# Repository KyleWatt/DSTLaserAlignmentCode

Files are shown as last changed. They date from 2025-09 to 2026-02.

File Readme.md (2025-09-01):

# Laser Auto-Alignment for FSOC Systems

Automated 3-axis alignment platform for Free Space Optical Communication systems using stepper motors and intelligent search algorithms.

## Features

- Sub-micron precision alignment (0.666μm steps)
- Dual search algorithms (Raster & Spiral scanning)
- Custom PCB controlling 12 stepper motors
- Real-time power optimisation
- 3D-printed mechanical components

## Hardware

- **MCU:** Raspberry Pi Pico 2350 B
- **Motors:** 12x 28BYJ-48 steppers with A4988 drivers
- **Power:** 12V input, 3.3V regulation
- **Materials:** PLA 3D-printed parts

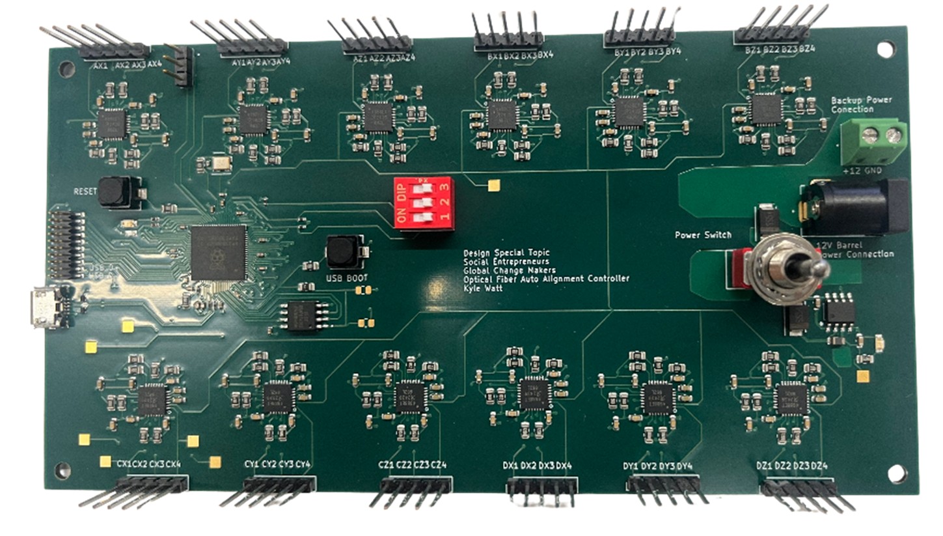
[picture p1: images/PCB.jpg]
PCB Image

*Custom PCB with RP2350B microcontroller and 12 A4988 motor drivers*

## Quick Start

1. Flash firmware to RP2350B
2. Assemble the mechanical system from the STL files
3. Connect via USB terminal (PuTTY/Tera Term)
4. Use the 'help' command for a detailed explanation of functions/commands
5. Run alignment algorithms: `raster`, `spiral', 'SPGD', or align with manual adjustments through manual mode or enter a control loop for continuous optimisation in automatic mode

### Manual Control
```
manual          # Enter manual control mode
centre          # Return to centre position
move x y z      # Move to specific coordinates
```

### Algorithms
```
raster <width> <height_shift> <iterations>
spiral <turns> <spacing> <points>
SPGD <iterations> <offset_range> <learning_rate> <threshold>
```

## Repository Structure

```
├── PCB/           # Schematics, gerbers, BOM
├── src/          # Firmware source
├── mechanical/    # 3D model files
└── docs/          # Detailed documentation
```

## Performance Results

| Algorithm | Starting Power | Peak Found | Improvement |
|---|---|---|---|
| Raster | -23.01 dBm | -4.89 dBm  | 18.12 dB |
| Spiral | -8.99 dBm | -6.21 dBm  | 2.78 dB |

## PCB Design

Custom 160mm × 80mm board with:
- 6-layer stackup for signal integrity
- Switching power regulation
- EMI mitigation design
- Test points for debugging

Design files and manufacturing documentation available in `/PCB` directory.

## Software Architecture

- **Dual-core processing:** Motor control + power monitoring
- **Struct-based design:** Position tracking and optimization
- **Memory function:** Automatic return to peak power positions
- **Real-time feedback:** Power monitoring during alignment

See [full technical report](docs/full_report.pdf) for detailed performance analysis and design decisions.

## Team

- **Kyle Watt:** PCB design, software development
- **Rory Mullen:** Mechanical design, prototyping  
- **Tamim Abdul Maleque:** Component sourcing, assembly

**Supervisors:** Professor Martin Lavery, Adam Vallance, Mark Main

*University of Glasgow - School of Engineering - 2024/25*

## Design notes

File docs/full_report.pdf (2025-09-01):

## ENG 5026: Design Special Topic 5 Laser Auto-Alignment for Communication Systems in the

Developing World.

## Report Written By:

Kyle Watt,
Rory Mullen,

## Tamim Abdul Maleque

2024/25

## Supervisors: Professor Martin Lavery, Adam Vallance, Mark Main

## Acknowledgment

We would like to extend our gratitude to Mark Main, Adam Vallance for their continuous support with technical support and laboratory guidance. We are also grateful to Professor Martin Lavery for the advice of the project and for allowing us to use the facilities of his Structured Photonics Group.

## Abstract

In this DST project, the development and evaluation of a compact, low-cost motorised auto-alignment platform for free-space optical communication (FSOC) system was designed to mitigate the effects of temperature and pressure fluctuations that impact the optical alignment of the fibres in the FSO system. A mechanical assembly done using 3D-printed PLA, which includes a X-Y flexure controlled a lead-screw mechanisms (which have a 0.20 mm pitch, hence a minimal step size of approximately 0.666 µm per rotation) using the, by the off-the-shelf 28BYJ-48 stepper motors and A4988 drivers for a automated alignment. A mechanical design connecting the Z-axis alignment with XY flexure was done using 3D-designed and printed runners, which also operated using a lead-screw mechanisms and used a cheap threaded steel 4-inch driveshaft. A purpose purpose-designed PCB was done where the Raspberry Pi Pico 2350 B microcontroller used a raster and spiral scan algorithm-based control to search and find the optimum power level. The raster and spiral algorithms were tested both to great success, with both scanning over areas with both high and low optical power before settling on the peak. This project shows that each of the algorithms is far superior to manual control at identifying and aligning the FSOC system with more precision.

## Contents

## Introduction

The internet is a vital need to billions of people in the world. Internet access fosters economic growth, security and technological developments in digital technology & artificial intelligence [1]. However, there is a stark digital divide globally, with an estimated 2.6 billion people remaining unconnected according to the 2023 press release article by International Telecommunication Union [2]. This divide affects developing nations because of the limitations of infrastructure and associated costs in deployment of traditional fibre optic cables, in geographically challenging or sparsely populated rural areas. As highlighted in the discussion on tackling Africa's digital divide, the capital cost of fibre can go upwards of US$100,000 per kilometre, which creates an economic barrier due to initial fibre infrastructure establishment [3].
Furthermore, even when deployed, fibres in remote regions can be susceptible to damage from environmental factors or theft, hence increasing the barriers for socio-economic progress. This limitation of connectivity necessitates the use and development of cost-effective alternative technologies to bridge the digital divide, using Free Space Optical Communication (FSOC).
Free Space Optical Communication (FSOC) transmits data through the atmosphere using beams of light, typically in the infrared (IR) spectrum, which is an alternative to traditional cabled solutions [3]. Conceptualised as ‘fibre optics without the fibre’ FSOC offers the potential for gigabits per second (Gbps) data rates [4]. This high capacity is due to the vast, typically unregulated bandwidth available at optical frequencies (Near IR region wavelengths: 850nm, 1310nm, and 1550nm). Therefore, the optical spectrum offers bandwidths that are orders of potentially tens of terahertz (THz) across various windows if compared to entire radio frequency (RF) spectrum, where individual services are allocated bandwidth typically measured in megahertz (MHz) or gigahertz (GHz). The RF spectrum is also often licensed by regulatory bodies.
The theoretical upper bound on the information rate that can be transmitted over a communication channel is given by the Shannon-Hartley theorem, which states that the channel capacity (C), in bits per second, is C=B × log2(1+S/N), where B is the bandwidth of the channel in hertz, S is the average received signal power, and N is the average noise power [5].Increasing bandwidth can increase channel capacity although not limitless as the relationship between signal to noise ratio is a constraint and other practical limitations such as power, dispersion and system integration need to be considered.
Recognising the potential of FSOC, the practical deployment of the systems is met with operational challenges. A primary concern, once an initial line-of-sight is established, is the maintenance of precise optical alignment between the transmitter and receiver [6]. The stability of this alignment is important for maintaining link performance, as very small deviations can lead to significant signal loss or complete link failure, especially as distance between transceivers increase. But, how are these issues arising? FSOC systems are susceptible to mechanical misalignments from sources such as thermal changes of mounting structures due to daily and seasonal temperature fluctuations, wind effects on buildings or structures where the equipment is housed and mechanical vibrations present in the physical world [4].
Narrow beam divergence which is inherent in laser-based communication makes precise pointing accuracy extremely important for FSOC. Pointing accuracy requirements can be on the order of several hundred microradians. Atmospheric effects such as turbulence (causing signal scintillation and beam wander) and attenuation due to fog or haze also impact long distance FSOC performance [4][6]. These atmospheric phenomena can cause the laser beam's intensity to fluctuate unpredictably, its path to deviate from the direct line-of-sight, and its overall power to diminish significantly before reaching the receiver, all of which degrade the quality and reliability of the communication link
Previously, for the FSOC set-up at University of Johannesburg, correcting such fine misalignments has required manual intervention, delicate screw adjustments using costly high-precision commercial components (Thorlabs XY Translation Mounts – costing approximately £170 each). This reliance on manual recalibration not only increases operational expenditure but also introduces delays in restoring connectivity, which impacts accessibility and scalability of FSOC solutions, especially in resource-limited settings.
To address the solution of mechanical misalignment and reduce costly manual recalibration in FSOC systems, this project focused on developing an entirely 3D printed compact, motorised auto-alignment system for XYZ axis. Using Commercial Off-The-Shelf (COTS) components to create the system accessible, affordable and easily replicable solution would hence democratise access to stable FSOC systems. Primary tasks of the auto-alignment use precise motorised control (using stepper motors), for fine adjustments. Such a system will operate in three axes:
- X-Y Adjustment: Provides angular correction crucial for coupling light into optical fibres (often with core diameters around 100µm).
- Z-Axis Adjustment: Optimises beam focus or collimation, vital for maximising received signal power, especially over longer distances where beam divergence is a factor.
The auto-alignment system is algorithm-based, that uses search patterns to locate and optimise the optical signal. Two common algorithms used in auto-alignment solution are Raster Scanning and Spiral Scanning [7] as depicted in Figure 1 below. Raster

Scanning is often one of the quickest methods for initially finding the beam at the receiver ("first light"). It operates by scanning along one axis (x-axis) and then indexing by a certain distance along another (y-axis), repeating this cycle. The advantage in this method is the utility for finding the threshold power detection (above -25dBm) and for subsequent search to find peak power optimisation. This method is limited to two-axis operation and involves discrete start-stop motions.
An additional method of Spiral Scanning executes an outward spiral motion, where it too can be used to find the first light in a larger general area of the beam and search for highest power position after completing the spiral. Continuous spiral scans offer smoother motion, where in computer programme the spiral code is described in polar coordinates (r, θ). This method is also limited to two-axis operation and requires completion of the entire trajectory described in space.

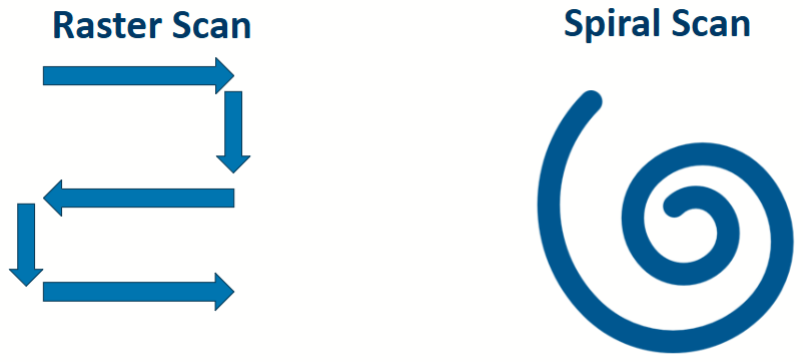
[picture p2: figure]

Figure 1: Illustration of search patterns used in FSO auto-alignment. (Left) Raster Scan Pattern and (Right) Spiral Scan Pattern.

The development of a cheaper and better commercially available auto-alignment solution makes FSOC a more practical as and sustainable solution for a more range of applications. For example, these portable self-aligning systems can be highly advantageous for providing emergency connectivity during disaster situations when terrestrial infrastructure is compromised [4] [6].
FSOC systems effectively address the "last mile" connectivity challenge, bridging the final network gap to end-users where fibre installation is often costly and complex [3][4]. Compared to fibre, deploying FSOC transceivers on existing structures like rooftops is less complex, and they can be integrated into hybrid communication networks with RF or fibre links to enhance overall reliability [3] [4]. These advantages enable rapid FSOC deployment, providing high-speed digital links to remote and rural communities while overcoming obstacles related to terrain, installation costs, infrastructure security and so bridging the digital divide [3] [4].

While transient obstructions might cause brief interruptions, the high bandwidth of FSOC links and multiple channels can mitigate the impact on many common internet activities. The deployment of such enabling technology also aligns strongly with several United Nations Sustainable Development Goals (UN SDGs), by fostering economic growth (UNSDG 8), promoting innovation and infrastructure (UNSDG 9), and reducing inequalities (UNSDG 10).

## Project Management

As a three-member team, communication was facilitated through MS Teams and WhatsApp, with a primary emphasis on in-person meetings. Work delegation was a collaborative effort, involving regular communication and consultation with supervisors, Mark and Adam.
Recognising the importance of early prototyping, the team initiated this process alongside printed circuit board (PCB) design. Electronic components were sourced with a focus on cost-effectiveness and global availability.
The Structured Photonics Group’s laboratory's 3D printing facilities were utilised for rapid prototyping and assembly of the mechanical system, enabling iterative testing and refinement. Algorithm work was completed in parallel with PCB design, ensuring that GPIO pins and electronic requirements were matched. The work was then performed in an optics laboratory on an optical table for testing of the full mechanical system with the algorithm written. A flowchart of the full process in this project is shown in figure 2 below.

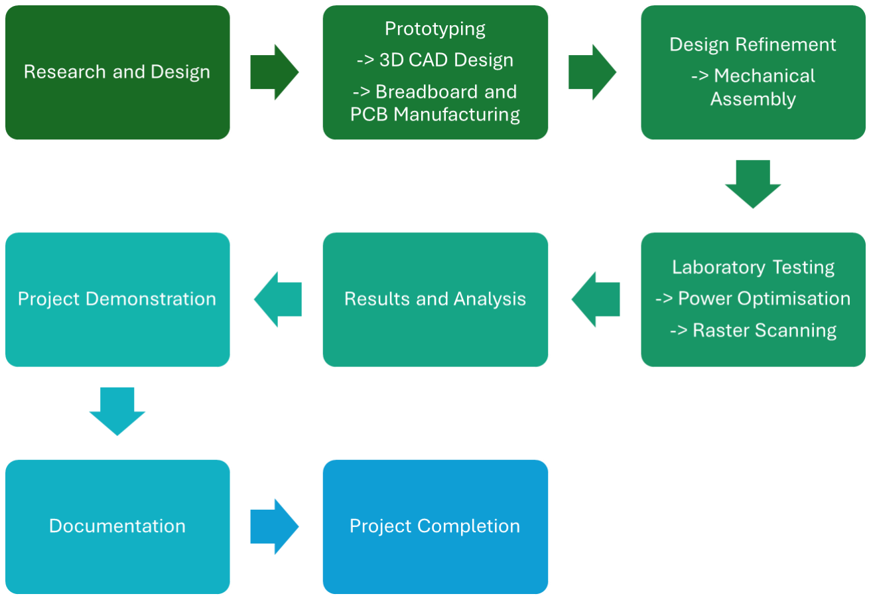
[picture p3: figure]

Figure 2: The Design Build and Test Project Flowchart of this project.

While the project successfully met its primary objectives, an area for improvement in project management would have been to maintain a more consistent pace of progress throughout the semester.

## PCB Design

## Requirements and Justification

The PCB was one of the earliest components developed in this project, based on the advice that manufacturing and debugging would require as much time as possible. A custom PCB was essential, as the project aimed to control four optical fibres' X, Y, and Z movements, requiring 12 motors. Without a PCB, the system would be significantly less compact, more challenging to assemble and maintain, and more prone to errors due to increased wiring complexity.
Additionally, designing a PCB made the system more reproducible. If successful, this design could be easily replicated and deployed by communities, providing them with internet access at a low cost and greater control over how that access is delivered.

## Components selection

One of the key criteria in selecting components for the PCB was ensuring that they were widely available and low-cost. This would make the design easily reproducible and affordable, allowing deployment in areas that cannot support the cost of traditional high-speed communication infrastructure.
Motor Driver
The first components selected were the motor drivers. We chose the A4988 stepper motor driver [8] because it was inexpensive (under £1) and readily available—both critical requirements. However, we encountered a challenge: each A4988 has eight input pins, and with 12 stepper motors, this would require up to 96 GPIO pins on the microcontroller - an impractical number.
To address this, we decided to minimise the number of active control inputs to each A4988. Pins that did not need to change dynamically were hard-wired to either high or low. Since micro-stepping was unnecessary, the associated pins (MS1, MS2, MS3) were grounded. Additional features such as reset and sleep were also deemed unnecessary, so these active-low pins were connected to 3.3V.
The only pins connected to the microcontroller were those essential for basic operation: step, direction, and enable.
➔ The step and direction pins are critical for controlling motor movement.
➔ Although not required for motion, the enable pin was retained to allow the microcontroller to turn off motors when idle, reducing power consumption, which was a key consideration for sustainability.

Motor
The selected motor was the 28BYJ-48 5V stepper motor [9], chosen for its low cost (~£6) and wide availability, both key selection criteria. However, a challenge arose: this motor has a unipolar configuration, while the chosen driver, the A4988, is designed for bipolar stepper motors.
Unipolar motors have a centre tap on each coil, allowing current to flow in one direction per coil half, which simplifies driving but results in lower torque. In contrast, bipolar motors lack a centre tap and require current reversal through each coil, making them more complex to drive but offering higher torque and better efficiency.
To address this mismatch, the centre tap (power) wire of the 28BYJ-48 was left unconnected, effectively converting it to bipolar mode, which allows it to work with the A4988 driver.
While the 28BYJ-48 does not offer high precision, this limitation is compensated by the mechanical design, which enables step sizes as small as 0.6 µm even without microstepping.
Power System
The power system used a 12V Barel jack input with a backup screw terminal, to allow it to be powered by a bench power supply. The 12V was adequate to allow functionality for the A4988 Stepper Driver, as it can function with load voltages up to 35V; however, all other components required a supply of 3.3V.
This meant the power had to be stepped down from 12V to 3.3V. To do this, we used the AP1509-33SG-13. The AP1509-33SG-13 was chosen as it is a switching regulator, meaning the energy loss to heat would be minimal. The other reason for selecting the AP1509-33SG-13 was its simplicity in converting to 3.3V from 12V, as it only required two capacitors, an inductor and a Schottky diode.
Microcontroller
The microcontroller chosen for this project was the Raspberry Pi Pico 2350 B. Again, the main reason for selecting this component was its low price and wide availability. On top of the low cost and wide availability, the Pi Pico 2350 B also has the added advantage of having 80 GPIOs, which is extremely useful for our requirements of 12 motors. An extra feature beneficial with the Pi Pico 2350 B was its ability to use multicore processing. This means that multiple processes can run in parallel; therefore, if any functions need to wait, they could be run in parallel and not block other processes.

Communication/Controls
Some final components that were added to improve the ease of use and future development of the board were DIP Switches, allowing for external control of operation and modes/algorithms used. It was also decided we would add a micro-USB port to the flash firmware of the Pi Pico 2350B to allow easy communication with external devices. TVS diodes were connected to the USB data lines (D+ and D−) to clamp high-voltage spikes caused by ESD or power surges, preventing damage to the USB transceiver or microcontroller. Since USB lines are exposed and can easily accumulate static electricity (e.g. from plugging/unplugging), TVS diodes help ensure reliable operation and extend device lifespan.
Simple LEDs were also chosen to help with debugging code and hardware. Also, male headers were connected to the motor drivers and GPIO pins to allow for external communications. All the other components chosen followed the previously mentioned components' datasheets.

## Schematic Design and Evaluation

The PCB was designed using KiCAD, a cross-platform and open-source electronic Design Automation Suite. The initial steps in the PCB design were to create a schematic.
RP2350B
The recommended design from the “Hardware Design with RP2350” [10] manual was followed when designing the schematic for the RP2350B, and all essential components for operation, such as the recommended oscillator and flash memory, were added following the manual. This can be seen in Figure 3 in the next page.

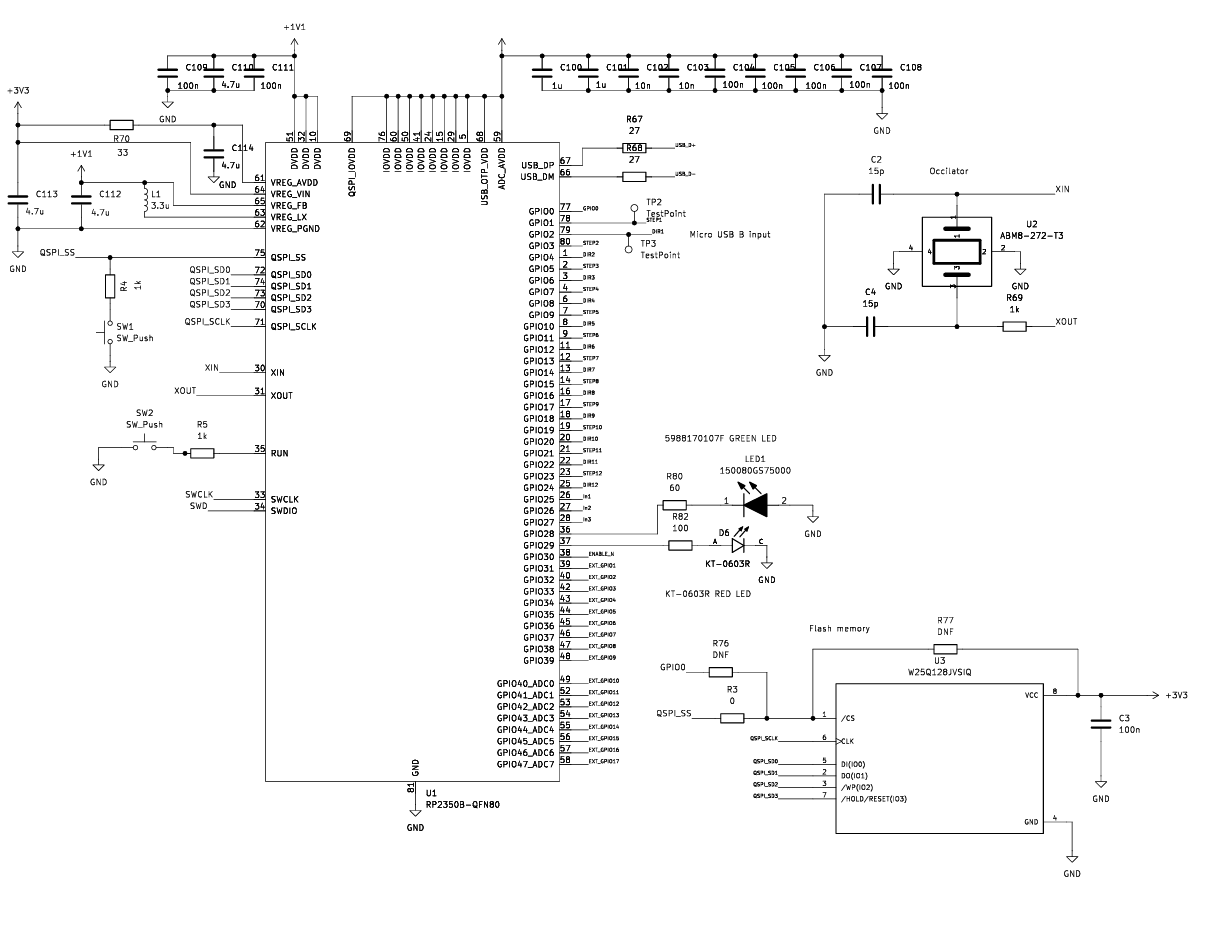
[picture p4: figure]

Figure 3: The 2RP2350B IC Schematic utilised in the PCB design.

As can be seen by Figure 3, the first 24 pins are used to control the step and direction of all motor drivers, and one pin, 30, is used to control the Enable function on all motor drivers. All other GPIOs were connected to allow external communication, such as buttons, LEDs and headers.
Motor Drivers
The next components are designed in the schematic, where the motor drivers are. As previously mentioned, the aim was to reduce the number of GPIO pins necessary to control the motor driver while still maintaining complete functionality. This was done by pulling all non-essential pins high or low, depending on whether they are active high or low. The A4988 was also configured to limit the maximum current to around 1 amp as higher current could potentially cause issues with the motors. This was done by configuring the reference voltage and sense resistors. In this case, the reference voltage (Vref) was 1.65V, and the sense resistors (RS), Sense 1 and Sense 2, were 0.2 Ohms.

Max Current =

Vref
8 × RS ≈ 1Amp (1)

All of which can be seen in Figure 4. The outputs of the motor driver OUT1A/1B/2A/2B were all connected to a male header, allowing for easy connection to the 28BYJ-48 5V Stepper Motor.

Figure 4: The Motor Driver 3 A4988 Schematic Design utilised in the PCB design.

Power
As previously mentioned, the majority of components required a 3.3V supply, and to achieve this, the AP1509-33SG-13 was used to step the power down from 12V to 3.3V. This followed the simple design outline in the AP1509-33SG-13 data sheet. However, a resistor and LED were added to indicate if the AP1509-33SG-13 was functioning as expected and producing 3.3V. Test points were also added all around the board in vital areas, such as the output from the AP1509-33SG-13, to help the debugging process. The test points were also added to other vital areas, such as the step and direction pins and the output from the A4988.

## PCB Design

Board Dimensions and Stack-up
After completing the schematic, it was reviewed with the assistance of Adam Valance and Mark Main. To ensure accuracy, all design elements were carefully evaluated and cross-referenced with the component datasheets.
Once the schematic was finalised, the next step was to design the PCB. I chose a
160 mm × 80 mm board size, as there were no constraints on dimensions. This provided sufficient space to accommodate all 12 motor drivers while also ensuring adequate separation between high-EMI components like the switching regulator and sensitive data lines like the USB D+ and D-.
The PCB stack-up used signal layers on the top and bottom, with a ground plane directly beneath each to ensure low-impedance return paths and reduce ground bounce. Two power planes were used to efficiently distribute 12V and 3.3V across the board; these power planes provide a low-resistance path for power delivery and help maintain stable voltage levels across the board. The close proximity of the power and ground planes also provided beneficial inter-plane capacitance, improving high-frequency power stability and reducing noise.

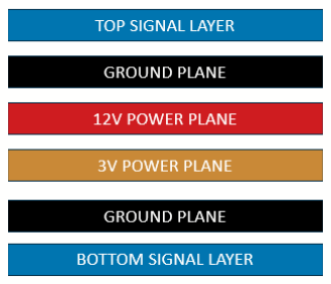
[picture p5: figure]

Figure 5: The 4 PCB Stack up showing the different layers of the PCB.

Component Placement
After the board had been traced out, the next step in developing the PCB was to start placing components. As previously mentioned, ensuring that components that produced a large amount of EMI were placed as far as possible from sensitive components such as USB data lines was crucial. Therefore, the switching regulator and USB connector were placed at opposite ends of the board, as shown in Figure 6 below. In addition to placing the switching regulator as far as possible from sensitive components to minimise electromagnetic interference (EMI), several other design choices were made to improve power integrity. One such consideration was the use of copper pours (fills) on the signal layer at the power input areas. If standard traces had been used instead of copper fill, the narrower width would have introduced higher resistance and inductance, leading to increased voltage drop and localised heating, especially under high current loads. By using copper pours, the current-carrying capacity is significantly increased, resulting in better thermal performance and reduced electrical resistance.
To connect the 12V input to the internal 12V power plane, multiple vias were used. This allowed for higher current-carrying capacity, reduced voltage drop, and improved heat dissipation. This is critical because if the via path to the 12V plane is too restricted for the required current, it can lead to localized heating, voltage instability, and in some cases contribute to increased EMI due to poor power integrity.
To further protect the power system, Schottky diodes were added at critical points. A Schottky diode was placed between the copper fill planes and the power switch, and another between the switch and the switching regulator. These diodes were chosen for their low forward voltage drop and fast switching speed, which are crucial in protecting the circuit from reverse polarity, back feeding, or inductive kickback when switching occurs. Their fast response helps clamp voltage spikes before they can propagate and damage downstream components.

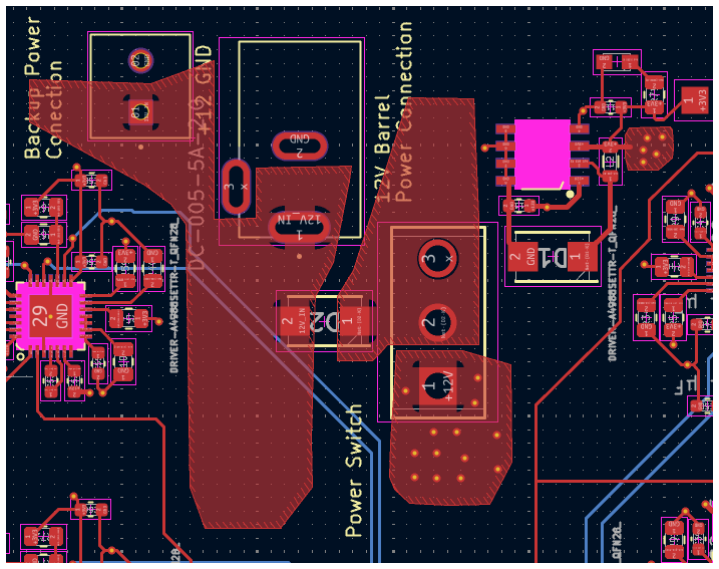
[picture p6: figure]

Figure 6 : The 5 PCB layout of the Power System

The stepper driver design followed the same design outlined in the schematic, only connecting vital operation pins to the GPIO of the RP2350 B. The motor driver outputs were connected to male header pins, which were labelled in a way to distinguish each optic/aperture and if it is to control the X/Y/Z for said optic, to make debugging and developing the code easier.
One key consideration when designing the motor driver layout was the placement of the decoupling capacitors. The decoupling capacitors were placed as close as possible to the power input pins of the motor driver ICs to minimise voltage ripple, suppress noise, and ensure stable power delivery during switching events. This design can be seen in Figure 7, and the same design was repeated for all 12 motor drivers.

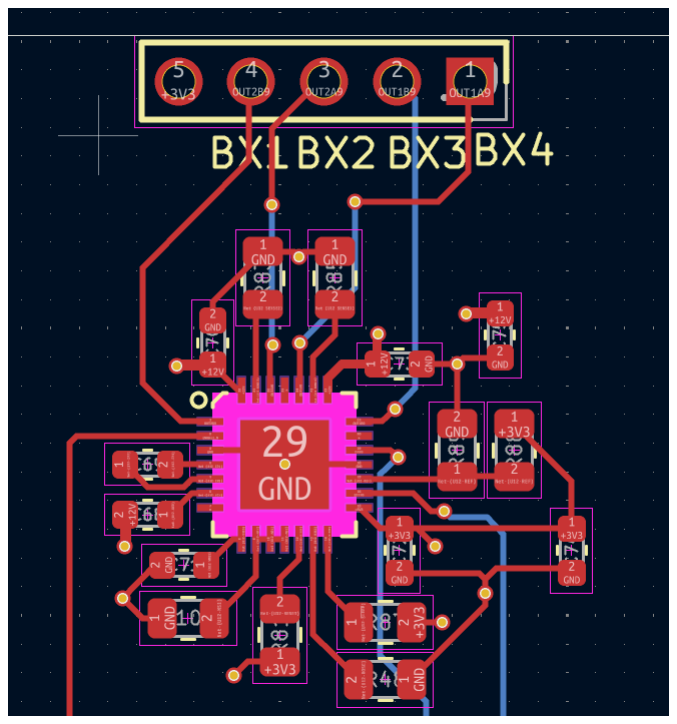
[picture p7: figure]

Figure 7: The 6 PCB layout of the Motor Driver

After all the motor drivers were placed and routed, the remaining key components were laid out and connected according to the schematic. One of the most challenging aspects of this stage was routing the fanout from the RP350B microcontroller. It was essential to place decoupling capacitors as close as possible to the power pins to ensure a stable voltage supply and suppress noise, as previously discussed. However, positioning them too close risked obstructing the fanout of signal traces from the adjacent GPIO and power pins.
This required an iterative layout process, carefully repositioning capacitors and adjusting trace routes to strike a balance, placing the capacitors close enough to be electrically effective while still allowing sufficient space for reliable fanout. Achieving this “sweet spot” was crucial for maintaining both signal integrity and power stability in the final design. Some other considerations were length tuning on the USB data lines. This is to ensure the data from the differential traces arrives at the same time, eliminating the chance of data corruption due to skew. Mounting holes were also placed in the corners of the PCB, enabling possible future integration into a compact system. The full PCB design can be seen in figure 8.

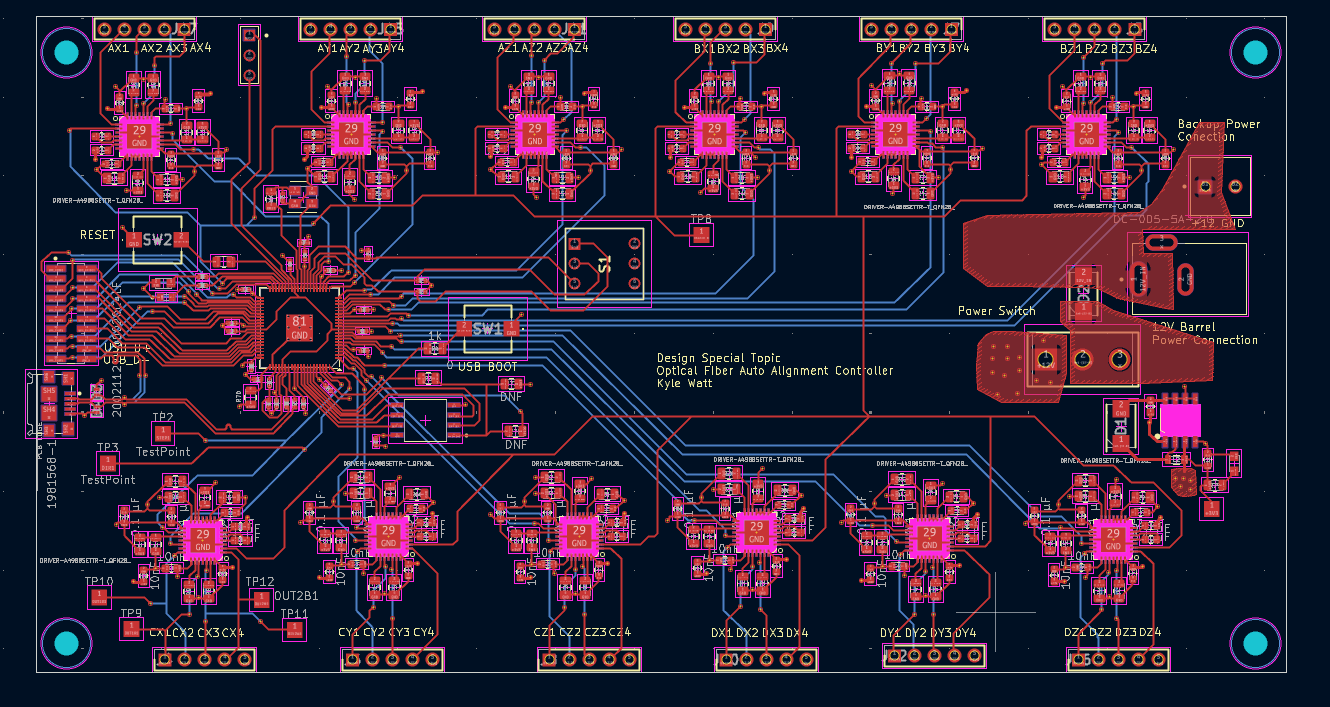
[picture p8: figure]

Figure 7 8 : The Complete PCB Design layout for the board.

## PCB Evaluation and Manufacturing

After the PCB design had concluded, the design had to be evaluated to ensure it meets the requirements and restrictions imposed to allow JLCPCB to produce the PCB. To do this, the design was first reviewed again with the help of Adam Vallance and Mark Main. To further investigate any possible issues that may arise when producing the PCB with JLCPCB, the PCB Gerbers, BOM (Bill of materials), and component placement files were run through the JLCPCB DFM (Design for Manufacture) check.
The JLC DFM check spots numerous errors in my design, such as silkscreen overlapping with pads. This is bad because it can interfere with proper soldering, lead to unreliable connections, and cause issues during automated assembly. Additionally, it may result in manufacturing delays or rejection of the board, and can obscure important component markings, making assembly and debugging more difficult. This meant I had to adjust or remove all the text and symbols that were below the tolerance of separation from pads. This was a long process as there were 1000+ points at which the silkscreen was too close to exposed pads, and some footprints had to be manually adjusted.
The spacing between traces was another issue found through the JLC DFM checks. JLC allows a minimum spacing of 0.15mm between traces. Anything below that may result in dry film breakage during electroplating, resulting in short circuits and lowering yield. Due to errors in my DRC (Design Rules Constraints), some traces had a spacing lower than 0.15mm, particularly the fanout from the RP2350 B. This meant all error traces had to be rerouted.
After all the JLC DFM checks had been completed, and they returned a good result. The BOM was checked, and the PCB was ordered.

## Debugging and Conclusions

After ordering the PCB, it took 2- 3 weeks to be manufactured and delivered. The completed PCB can be seen in Figure 9 in the next page. The PCB did not switch on immediately. Therefore, the debugging process began. The first issue found was that the output from the switching regulator, supposed to be 3.3V, was actually around 1.2V. This was due to a mistake in the bill of materials, where instead of ordering the AP1509-33SG-13, which has a fixed output of 3.3V, the AP1509-SG-13 was ordered, which has a variable output dependent on a voltage divider connected to pin three, the feedback voltage pin (Vfb). The equation to calculate the output is shown below.

Vout = Vfb × (1 +

R1
R2

) (2)

Since the board was designed to use the fixed switching regulator AP1509-33SG-13, it did not include the necessary voltage divider to control the output to 3.3V. This meant that Vout = Vfb, and since Vfb is 1.23V in the adjustable version, the output voltage was only 1.23V, far below the intended 3.3V, rendering the power supply inadequate for the components operating on 3.3V.
To resolve this issue, a 1.6K resistor R1 and a 1K resistor R2 were connected to pin three to form a voltage divider, enabling the switching regulator to output 3.3V.
After the issue with the switching regulator was resolved, the board was able to supply 3.3V to all necessary components. However, we were still unable to establish a connection with the RP2350 B. This could be due to many reasons, such as components being placed in the wrong direction, for example, a diode, which would block signals from reaching their intended destinations. However, due to time constraints, the decision was made to leave debugging the PCB to a later date and focus on the software side, creating a working prototype using breadboards, as having a working auto alignment system was more important than a working PCB at this stage. I am confident that with more time to debug the PCB could be integrated into the system.

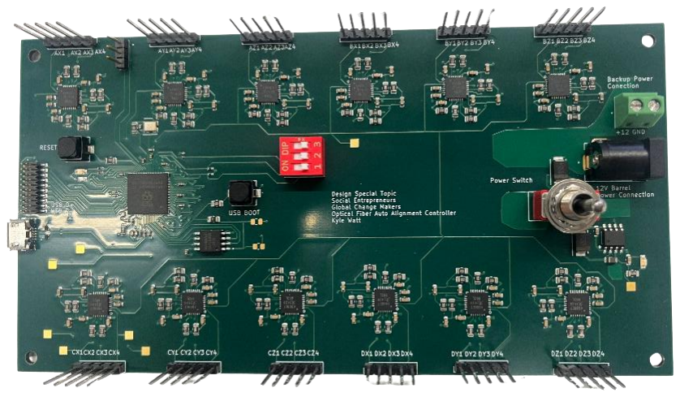
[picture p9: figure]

Figure 9: The 8Manufactured PCB from JLCPCB.

## Mechanical System Design

Alignment of the laser beams is only possible with an adequate mechanical system. This design must allow directional movement in the X, Y and Z directions. It must also be precise in its movements and not generate excess instability as this would be detrimental for alignment of fibres. Due to how sensitive the fibres are to external factors such as turbulence, wind, rain, the mechanical system must not add to this in any way. This system was therefore designed so that it would be able to be implemented onto the already existing FSO structure that was built, and operating, due to previous work within the lab group. This project made use of the CAD modelling software Autodesk Fusion as the design of the pre-existing flexure system was readily available within this medium. By designing with this 3D model the preciseness of the implementation could be maintained. All components within this mechanical design were 3D printed with PLA material which is readily available for ~£15-20. Similarly to those components chose within the hardware design this helped maintain the accessibility and affordability of this system, crucial for implementing this optic system into the developing world.
X- and Y- Axis Movement
As mentioned previously this mechanical design integrates with an already existing optical skeleton so that alignment automation can be implemented. The first step within this process was allowing for X and Y directional movement. This was made very simple due to the already existing 3D model which could do so.

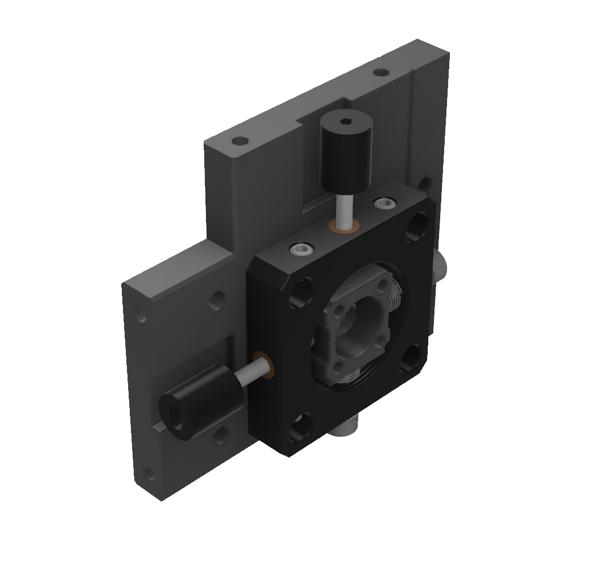
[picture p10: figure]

Figure 10 shows the final flexure that was used within this mechanical design which features an extended face for the Z-axis system to connect (more on this later). From the leftmost image the details of how the beam is moved can be understood. The socket within the centre is the point at which the fibre attaches, where light is transmitted and

Figure 10 : X and Y Flexure with Hex Nuts for Stepper Motors for Alignment received within the communications system. This socket is loosely connected to the rest of the flexure and held in place with springs on adjacent sides. On opposite sides of the spring the lead screws responsible for incorporating movement of the flexure are seen. By rotating these lead screws (+) or (–) movement along the respective X and Y axes is achieved.

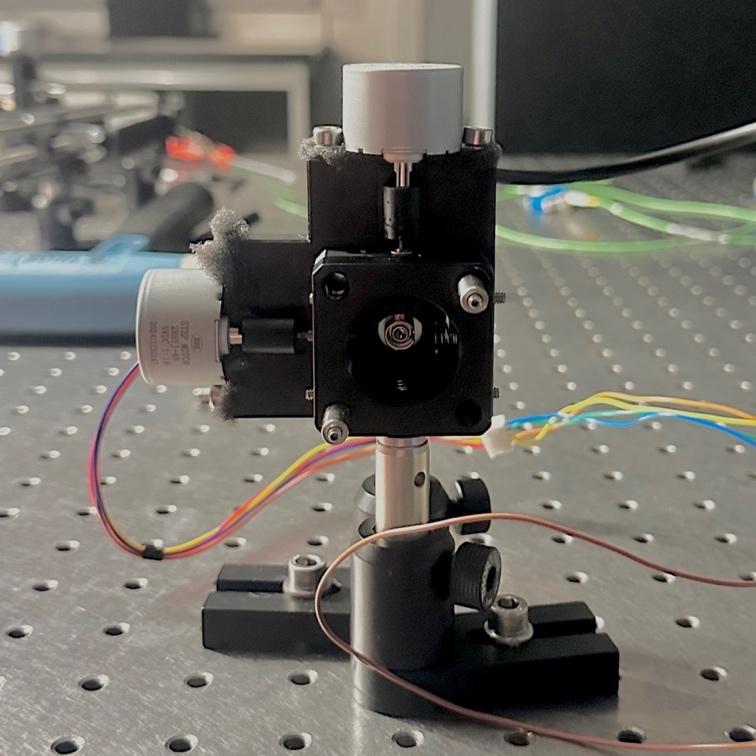
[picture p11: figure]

From the above Figure 11, the physical implementation of the X-Y flexure can be seen with the stepper motors present. This design was largely successful with extremely precise movements in both X and Y directions. This was due to the lead screw having an extremely shallow pitch at 0.20mm. The motors which were working in their full step operating took 300 steps in the algorithm to complete a full rotation meaning that 1 step would give a change in direction of approximately 0.666μm. This shows there to be extremely tight control over the change in alignment and is most definitely a benefit of this system over the manual alignment system previously done by hand allowing for more precision.
The system, however, does have some drawbacks. During setup there are some areas which require attention particularly when ensuring that the lead screws are properly threaded and that the socket lies in the centre of the flexure. As only the aperture at which the socket is attached can move, there are points at which no more movement can be achieved in both X and Y directions. If the flexure reaches this point where, for example, X is maxed out, then no further changes in this direction will alter the alignment. This can however cause the lead screw to either unthread itself from the bushing, or thread itself through the bushing leading to the protruding and eventually detaching. It is therefore

Figure 11: 3D printed X and Y Flexure with Stepper Motors Connected for Alignment Control essential that the fibre is centred first so that the maximum number of steps in all directions can be ensured. The distance from the minimum to maximum X and Y locations was estimated to be roughly 5000 steps, this gives nearly 17 full turns of the motor before no further changes will be seen. It was still difficult to find the centre of the flexure however and if this was not properly aligned to begin with it was very easy to cause issues with the screw. Implementing end stops at the absolute maximums of each direction would be extremely beneficial when going forwards with future designs. Having end stops for the lead screws would also allow for a more exact centre point to be found in future.

## Z - Axis Movement

Why it is Necessary
To add further configuration when aligning the laser beams it was decided that the addition of Z-axis movement of the optic would be beneficial. By using a collimation lens to pass the infra-red laser through but moving the z-axis further away or closer, then the beam can be expanded or focused, respectively, whilst maintain collimation. By doing so a decrease in divergence can be seen over the network. Mock data was produced using a python script to show the difference in a tightly focused small diameter beam, and an expanded larger diameter beam.

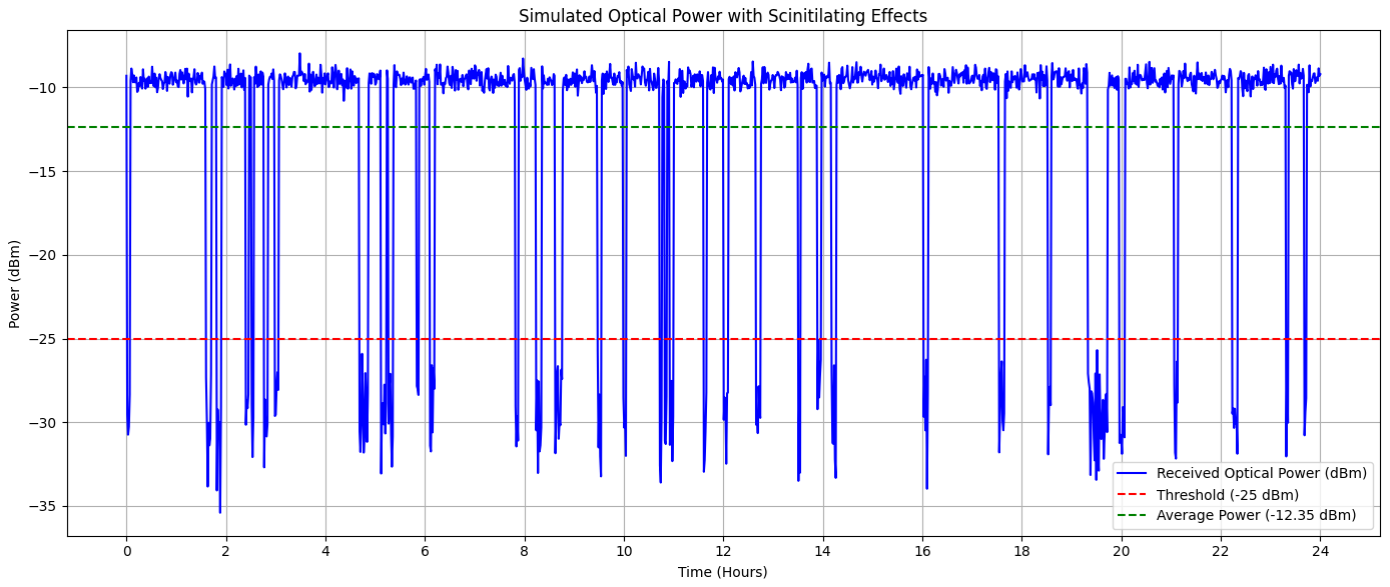
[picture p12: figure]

Figure 12 shows how the beam in a free space optic system may behave when operating at a very sharply focussed beam which is in alignment. Over the course of the 24 hours within a day the communication system experiences multiple large-scale dropouts at which the power received drops below the threshold power. For this simulated system the threshold power is the value at which an adequate connection to the network will be observed. With this system frequently dropping below that value it could be said that due to the small diameter of the beam the system is overly sensitive to changes in the

Figure 12 : Mock Data of a Small Diameter Beam Which Exhibits Scintillating Effects environment that it is situated. With turbulence, rain, and fog possibly causing alterations in the alignment with a beam with such a small diameter the margin of error is extremely small. The size of the beam not only alters the size of the beam transmitted but also the size of area of which the fibre will accept light over. With a small beam this area is extremely small but by increasing this area through movement of the z-axis this may be improved.

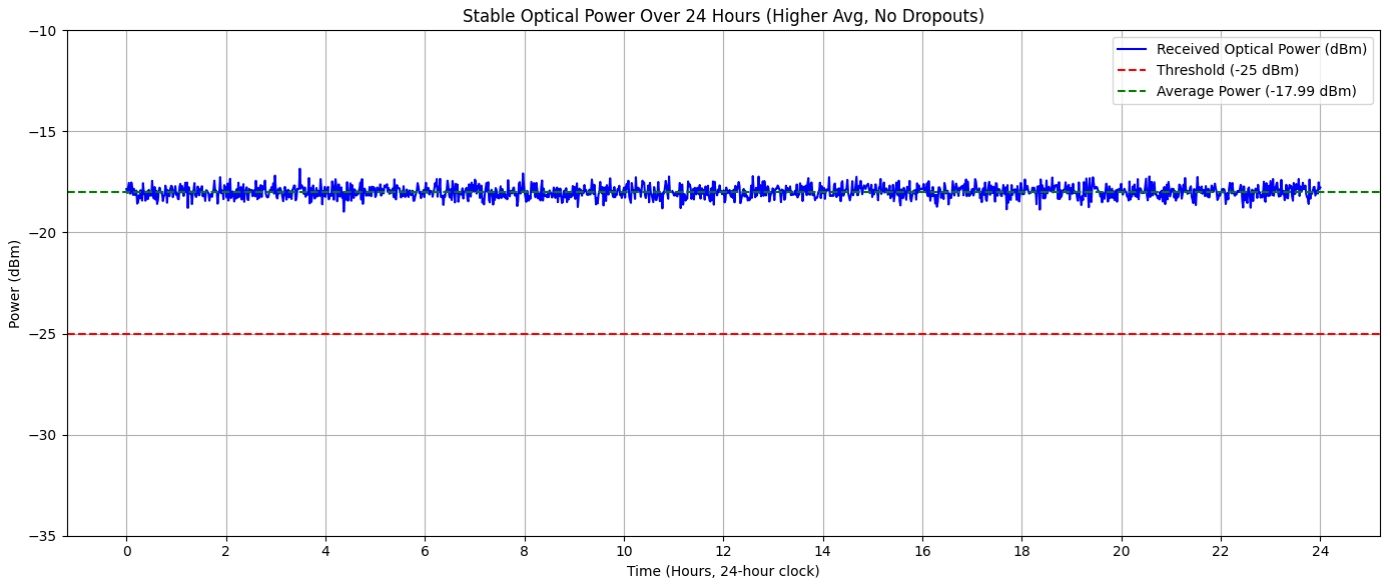
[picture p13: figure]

From this representation the effects that widening the beam may have for an aligned system can be seen. The power of this system has dropped quite considerably slightly closer to the threshold of -25dBm. Despite this though the trace is extremely stable and does not readily drop to below the threshold maintaining a stable connection for the network. This is due to the mitigation of the effects which external factors are having on the alignment of the laser with the larger beam being able to catch some power from the

Figure 13 Mock Data of a Larger Diameter Beam with Stable ConnectionFigure 13 9 Mock Data of a Larger Diameter Beam with Stable Connection

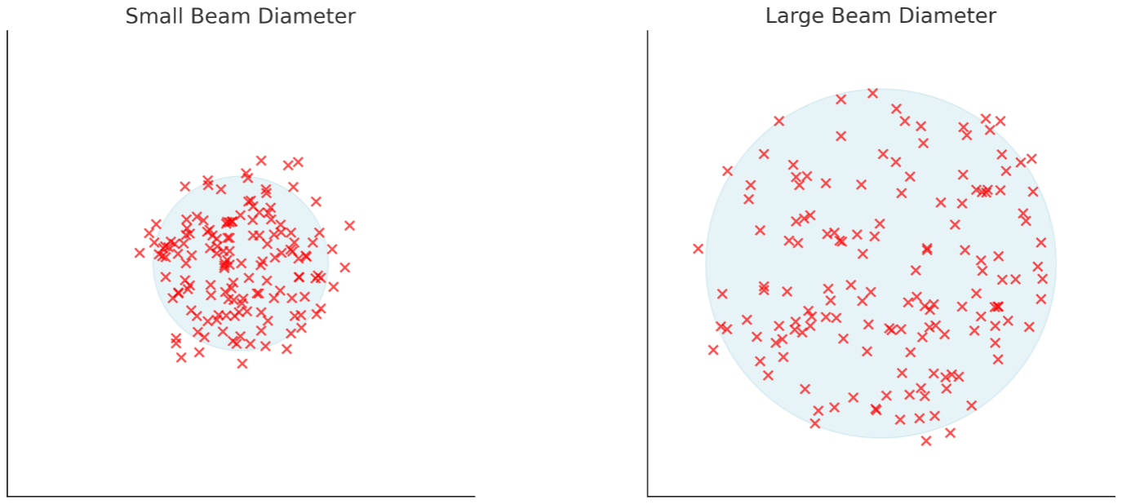
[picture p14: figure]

Figure 14 Effects of External Factors on Optical Alignment for Smaller and Larger Beams other size due to more overlap. This idea can be visualised better below, again this data is just for representation.
The small beam diameter observed shows as expected more points at which there is a complete loss of power. This is almost completely minimised in the larger beam diameter where even with larger movement of the alignment, connection can still be maintained.
Mechanical Design of the Z-Axis Alignment System
Moving on from why z-axis control is beneficial for aligning the optical system it will now be explained how this project aimed to do so through mechanical design. Again, this movement was controlled using a stepper motor and all parts, unless stated, where 3D printed with PLA. Initially, the concept for moving the fibre in the z direction was based upon having a bracket that would push/pull the XY flexure discussed earlier which would be mounted on the cage rods of the optical system. This however was changed due to the friction between the flexure plate which was quite rigid in its design and the cage rods making for unstable adjustments of the z-axis.

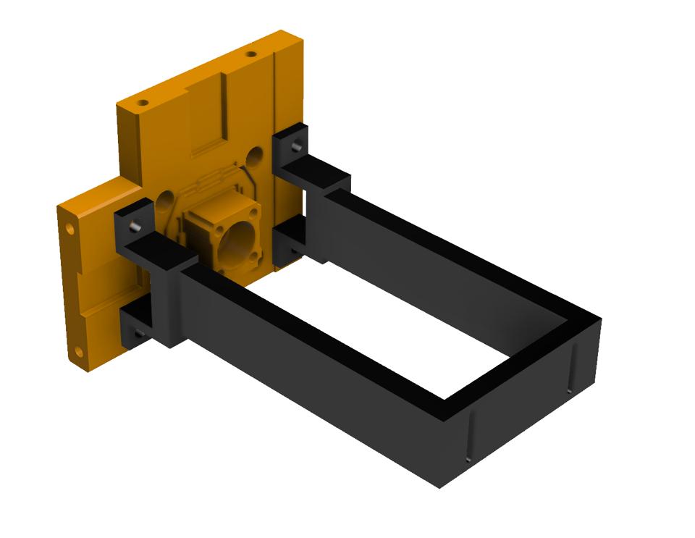
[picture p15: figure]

The design was then altered so that the flexure would no longer be mounted on the cage rods which cause issues when attempting the slide along these. Instead, it would be the z-axis bracket which would be on the cage rods acting like a runner along these whilst supporting the weight of the XY flexure. To achieve this a redesign of the bracket was underwent to allow for the runners, and an increased strength so that it would support the weight of the flexure without introducing any bowing into the system which would in turn be detrimental to the alignment of the fibres.

Figure 15 Initial Z-Axis Bracket Concept: Changed Due to Friction Between Cage Rods and Flexure

Figure 17 shows the final design of the z-axis bracket which show differences from the previous iteration. The runner concept that was mentioned can be witnessed with two runners on the bottom of the bracket and one on the top. As well as providing a clear path for the z-axis alignment system to travel along the cage rods these bars act as strong supports that are capable of weight bearing. By having runners on both the top and the bottom of the bracket the system is locked in place and there should be minimal to no tilt at the flexure as the weight of this is compensated for. The 3rd image in the figure shows the XY flexure connected to the bracket like before with screw points forming strong connections.

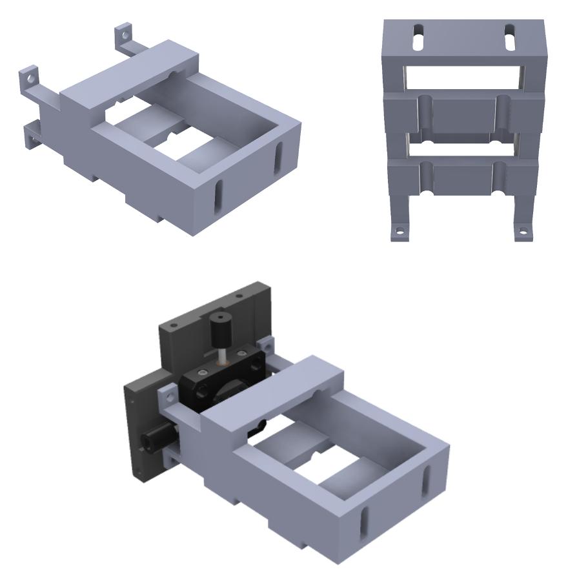
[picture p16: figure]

Figure 16 Z-Axis Bracket: Final Concept with Load Bearing Runners

From this point onwards with the flexure capable of movement in the z-direction it was now essential to automate this movement by using the stepper motors and alignment algorithm. The mechanical system for this had a few separate parts that worked together to turn the rotational movement that was generated from the motor into lateral movement that could move the Z-bracket and flexure farther and closer to the lens, broadening and narrowing the laser beam.

The full assembly of the system is seen in Figure 17 so that a better understanding of how the individual components are supposed to work. The bracket is shown sitting atop of the cage rods making use of the runners implemented previously and is seen to. Be connected to the X-Y flexure. From this stage the focus shifts towards the back end of the system where the stepper motor is situated. This is mounted using two brackets that are adjustable at top and bottom where they connect to the cage rods so they can be fixed or unfixed. For this system they are unfixed and capable of movement.

ure 10 Entire Labelled Mechanical System with Particular Focus on the Z-Axis Alignment SystemFigure 11 Entire Labelled Mechanical System with Particular Focus on the Z-Axis Alignment

Figure 17 Entire Labelled Mechanical System with Particular Focus on the Z-Axis Alignment System

The stepper motor is attached to a 100mm M4 threaded steel rod which is used as the main driveshaft for the lateral movement.
By using the algorithm and stepping the
motor in clockwise steps the rod will also
rotate clockwise. This will travel through the fixed nut that is seen in gold. The two plates that are seen have a gap directly in the centre which allows for the rod to pass through, sandwiched in between these two plates is a M4 nut which does not have the clearance in the gap to be displaced. Once these two plates are fixed together and tightened so that they are fixed upon the cage rods, threading of the driveshaft through clockwise will then result in forward movement of the stepper motor as well.
Figure 20 then shows how this forward/backward movement of the motor stage through the fixed nut position also allows for the movement of the flexure. Long beams that are mounted on the same bracket as the motor are also connected to the z-axis bracket. This means that when the motor moves forward these push the bracket, and when these move back the beams pull the flexure. This results in the lengthening and shortening of distance from the optical fibre till the collimating lens which manifests as broadening and
narrowing of the radius of the laser beam.
To get a visualisation of whether the z-axis

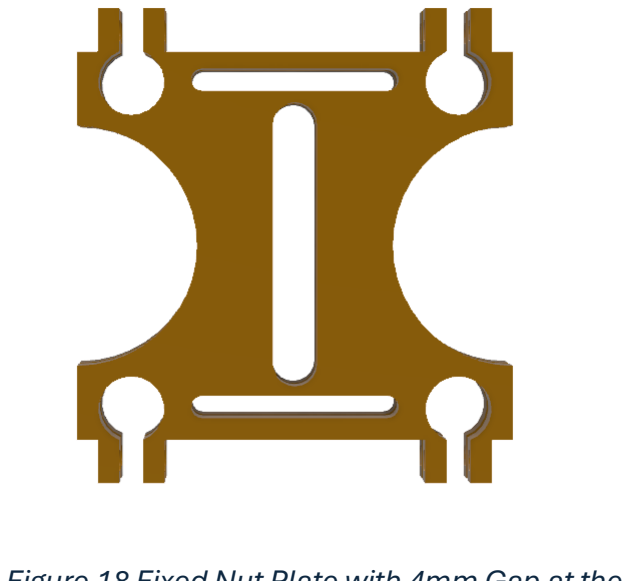
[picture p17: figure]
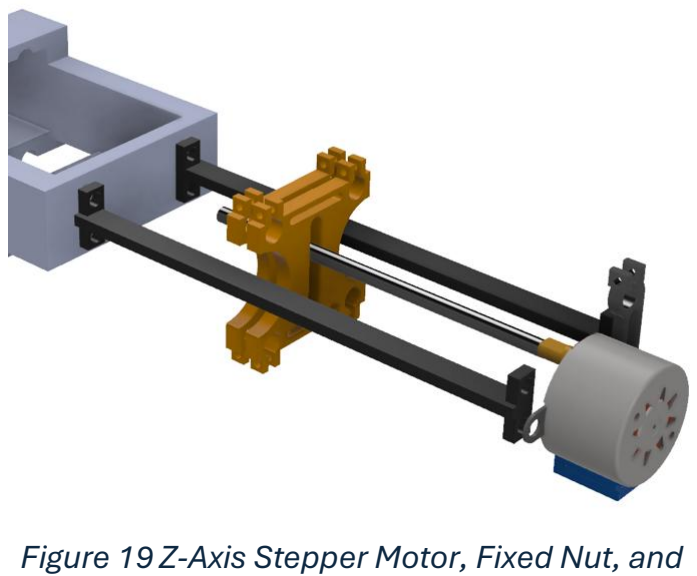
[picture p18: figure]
Adjustable Cage Rod Fasteners

stage was working adequately, the laser was shone over a larger distance so differences in beam size could be perceptible. From the two images in Figure 20, which are stills from the same video, it can be observed that by rotating the motor clockwise, the laser beam reduces in diameter and becomes more focussed on the target. This is due to the lessening of the distance between the optical fibre where the laser is generated and the

Figure 18 Fixed Nut Plate with 4mm Gap at the Centre for the Driveshaft, Screw Holes at the Top and Bottom for M2 tightening, and

Figure 19 Z-Axis Stepper Motor, Fixed Nut, and Bracket Connected by Large Push/Pull Beams lens where collimation of the laser occurs so that the laser can be transmitted. If the distance is less, then the spread of light is also less before it collimates.

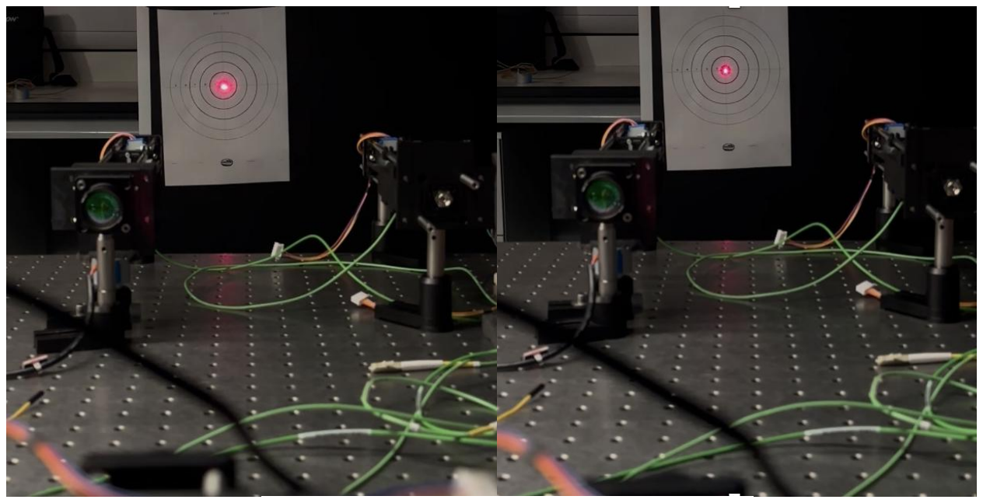
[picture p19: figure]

The representation of the laser beam increasing in diameter and decreasing in diameter shows that the z-axis mechanical alignment system was a success. This is because it integrates well with the already existing system and can move the flexure in both z-directions resulting in alterations in the diameter of the laser beam. Further improvements could be made to the design by making it slightly smaller in scale. Due to the size of rods used, at 100mm, the system needed to be scaled accordingly. However, the system could be drastically reduced if the size of threaded rod was decreased. The fixed nut system could also be simplified into one plate with one fixed nut position that is not adjustable for future iterations of the design.

Figure 20 Diameter of Laser Beam Reducing as the Z-Axis Alignment System Moves

## Software

## Software design

The goal with designing the software for this system was to create a method to accurately move up to 12 motors at once and track all motors' positions, allowing for the best point of power to be found.
The current software functions off of a command line user input, as this was found to be the most efficient way of debugging the code and testing the alignment algorithms, as it lets a user control the movement of all the optics easily and allows for easy iterative testing of the algorithms with custom variables. A software flow chart describing the implementation can be seen in Figure 22.

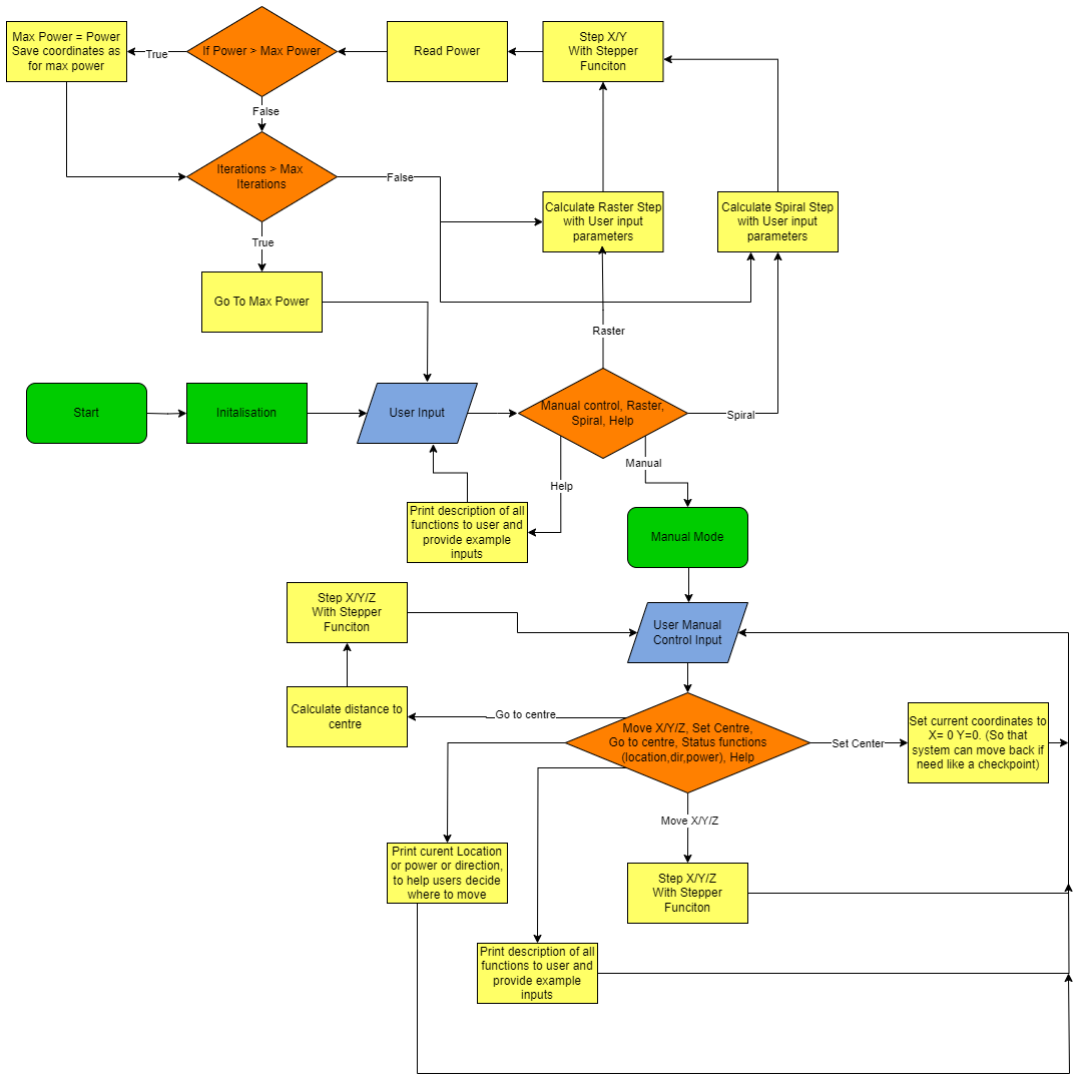
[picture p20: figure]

Figure 21: Software Flow Chart

## Main Loop

The first step in the software is to initialise all input and output, enabling
communication with external components. The software then enters a continuous loop of checking for user input commands to transmit through a command line interface, such as PuTTY or Tera Term. The software then parses this user input, and depending on the command, executes the necessary functions.
If the user enters a command to manually control the system, it switches modes from main to manual control. The manual control loop functions in the same fashion as the main loop; however, it checks for different commands, allowing the user to control all axes for every optic.
While in manual mode, users can also set the location that the optic is centred and use a command “centre” to go back to this point at any time. This helps overcome one of the main issues when manually aligning the optics. If done by hand, it is impossible to get back to exactly where you were previously, which can cause challenges when aligning. It is always tempting to continue moving to try and get a last small increase. However, this might cause a dramatic loss of power, and if the user was aligning the laser by hand, they would not be able to get back easily to where they previously found good power.
The manual alignment takes more time than the algorithms and requires user input and decision making, however, it can be extremely useful when initially aligning the laser.

## Stepper

To implement the movement of motors, a struct-based stepper function was created. The stepper function used two main structs, one for Optics and one for motors. Each optic struct contains its current X, Y and Z coordinates, the coordinates where the optic had best power, the optic's best power and also 3 motor structs for each axis motor. The motor structs contained each motor's current steps, target steps and a Boolean value of whether it was moving or not. This allowed the system to know what motors needed to move and for how many steps. It also made it easy to go back to where the maximum power was found.
To move the motors, a function called “motors_move()” was created. It had the task of checking what motors needed to move and then sending the high-low pulse to the motor drivers to initialise a step. However, this function does not just step each motor individually, as that would be extremely inefficient. For the motor driver to recognise a step, it requires the signal to hold high for a short period of time, then hold low for a short period. Therefore, to step, the system must wait for an adequate time period for the stepper to recognise a step, while waiting, the system cannot execute any other operations, this is called blocking and should be minimised as it is inefficient. If the system had to wait when stepping each of the 12 motors, it would be blocked for a long time and extremely inefficient. That is why the stepper function operates as follows:

MOVING = TRUE IF ANY MOTORS NEED TO MOVE
WHILE MOVING = TRUE
FOR OPTIC IN LIST OF OPTICS
FOR MOTOR IN EACH OPTIC
IF CURRENT MOTOR STEPS NOT EQUAL TO TARGET STEPS SET STEP HIGH

HOLD HIGH FOR TIME PERIOD
SET ALL STEPS LOW
HOLD LOW FOR TIME PERIOD
This means that instead of waiting up to 12 times, the system only has to wait once to step all motors. After each step, the stepper function then compares the new power levels to the previous maximum power, if the new power is better, it then saves that as the maximum power and saves the coordinates to achieve the maximum power allowing it to go back to where it had the best power, whenever the function “go_to_max_power()” is called.

## Power

The power of the system was read from Adam Valance and Mark Mains' previous project. The power values were first sent as a string through USB and captured on a PC through Python. The Python application allowed for some data manipulation, where start and stop bits were added to the string to make parsing the power easier for the system. The power was then transmitted to the RP2350B through USB. However, since the RP2350B only has one USB port, and that was occupied with receiving commands from the user input command line and sending back responses, it could not be used to also read the power data. Therefore, a USB to TTL Serial converter was used. This meant that the power data could be read over any GPIO pins on the RP2350B that were initialised to receive UART communications.

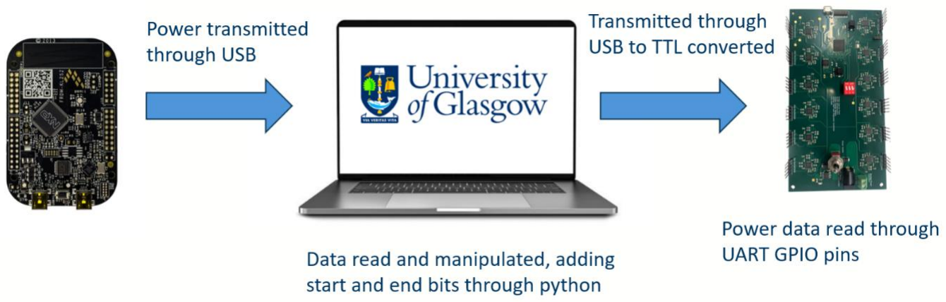
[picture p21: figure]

Figure 22 : Power reading flow chart

One other issue that arose when reading the power data was the frequency at which the power data was being transmitted. Originally, the software would clear the UART communications buffer, then wait for the start of a new packet by searching for a start bit. That way, the current power would always be the most recent. This would allow for the power to be checked after each step. Therefore, the system would know the exact power for each step. However, since the frequency of power transmission was relatively low compared to the desired step speed, this option was not practical. It would require the step speed of the motor to be bottlenecked by the frequency of the power meter, which was less than 5Hz, and since each step is around 0.6um, the system would take too long to practically test its performance. For reference, the algorithms that were tested, discussed in the next section, require more than 10,000 steps.
Therefore, a new method for reading the power of each optic had to be implemented. This is where the RP2350B's second core was extremely valuable. The RP2350B has two cores, which means that different processes can be run in parallel with each other on each core. This meant that the second core could be used to constantly read and parse the power data, without interfering with the main operation. The second core constantly reads and updates the current power for each optic. The power of data is saved in a power struct that can be accessed by other parts of the system through mutex locks. This means after each step, the stepper can compare and find its current power. However, it is not 100% accurate, as previously mentioned, the stepper steps faster than the power data is transmitted. Therefore, the system will see the same power for multiple steps. It would be best for the stepper to know the exact power after each step; however, for this project's initial development and testing, with the constraints of the power data transmission frequency, this was found to be the most optimal solution.

## Raster and Spiral Algorithms

The Raster and Spiral algorithms were simple functions that would take in user parameters and calculate a search path for the optic to follow. The raster scan requires the user to input the width of the scan, the shift in height after each iteration and the number of iterations. It then calculates the target steps for each optic and calls the previously mentioned motors_move() function to step all necessary motors. When the raster scan reaches its maximum number of iterations, it then goes to the point at which each optic has its best power.
The Spiral algorithm functions in the same way, however, it requires different user inputs. The spiral algorithm requires the user to input the number of turns the spiral should have, the spacing between each turn and the number of points the optic should go to along the spiral path. The more points, the smoother the spiral path. Just like the Raster Scan when reaches its maximum number of iterations, it then goes to the point at which each optic has its best power.

## Software conclusions

In conclusion, the software developed met its main aim of being flexible and easy to work with, offering the ability to precisely align multiple optics at once and perform search algorithms to find the best power on every optic. However, there are some downsides to this software. As previously discussed, the accuracy is lowered from stepping faster than the frequency of the power meter.
One other weakness in the current software is that the algorithms only search a predefined path; they are unaffected by how the power changes as they move, leaving huge room for optimisation with the integration of more intelligent algorithms. Lastly, the current software set-up requires constant user interaction and decision-making. If this system were to be implemented in a real-world scenario, this setup would be extremely impractical.

## Future Software Developments

As mentioned in the conclusion, there are multiple aspects of the software that could be developed if this project were continued. The first being the need for constant human monitoring and interaction. As previously stated, this would be impractical if this design were implemented in a real community. Were this design to be implemented in a real community, the system would have to decide for itself what optics should be using algorithms to search for better power and what optics to keep stable as a safety, in case any moving optics were to experience a dropout. This would require a control system to be developed, the software flow chart of which might look similar to the one shown in Figure 23.

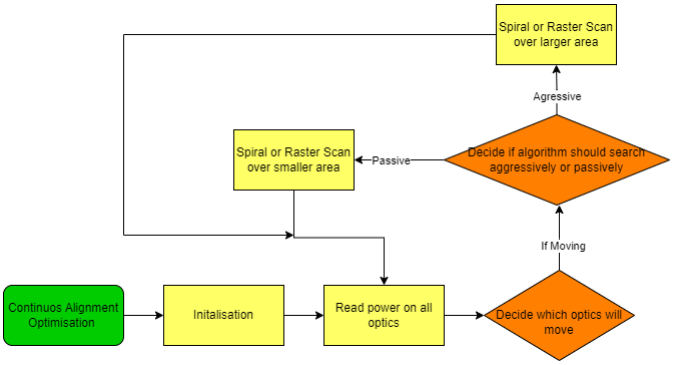
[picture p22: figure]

Figure 23 Future Software Flow Chart

Also, previously mentioned in the conclusion of the software was the possible optimisation with using “smarter” algorithms that could change the path of the optic depending on current and predicted future power, as current algorithms only follow a path predetermined without any context of the performance of the system.
Another area of improvement for the software would be increasing the frequency of power data. allowing the system to adjust and step at a high frequency without sacrificing accuracy by relying on out-of-date power data.
Lastly, one other area of possible improvement would be software that could initially align the laser, as currently the raster scans and spiral can only find the best power after they have already been manually aligned to a close enough proximity to allow good power values to fall within the algorithm's search area. This would most likely require extra information, for example, some type of IR sensor and computer vision and most likely also require adjustments to the mechanical design, to allow more freedom of movement to make larger adjustments when misaligned.

## Results and Evaluation

This section will detail results that were gathered from the two alignment scans that were implemented by the algorithm. This data was extracted by logging the entire sessions from the serial communication software PuTTY that was used to command the algorithm and begin scans. By printing the X location, Y location, and power readings at these points, a picture could be built up of the physical scan. The success of the individual algorithms could then be assessed through ensuring that the pattern was correct and that the point of most power was evaluated and subsequently moved to.

## Raster Scan

The first of these algorithms that was tested was the raster scan that has been previously mentioned. This can be seen in Figure 24, where the pattern of scan is apparent.

The plot shows the raster starting from the bottom left corner at the start of the scan and travelling along in a serpentine fashion. The parameter set for this scan were for the X-steps to be 500, the Y-steps (at the end of each row) to be 20, and the scan to run for 10 iterations. The graph is annotated with specific points including the peak and the minimum power observed over the scan. The disparity in these numbers can be seen with the minimum of -29.21dBm representing a very poor power for this system, almost a complete loss in connection, to a peak of -4.89dBm which is an exceedingly good connection for what was being tested. This highlights just how sensitive this optical

Figure 24 Results of the Raster Scan Algorithm Starting at a Power Reading of -23.01dBm Observing a Minimum of -29.21dBm and Finding a Peak of -4.89dBm system can be at times with even small adjustments of the stepper motors changing the power value vastly. This shows the necessity of precision within the alignment system, which is present in this project; without it, it would be exceedingly difficult to manually align to a peak value similar to the -4.98 dBm seen here. Another point worth noting is the point at which the scan pattern has ended, at the top left corner. The algorithm stores the point at which the power is the highest, then instructs the stepper motors to move back to the position where this power was observed. The plot shows this in action with the plot darting diagonally down and across to the point at which the system settles into having its new peak power.

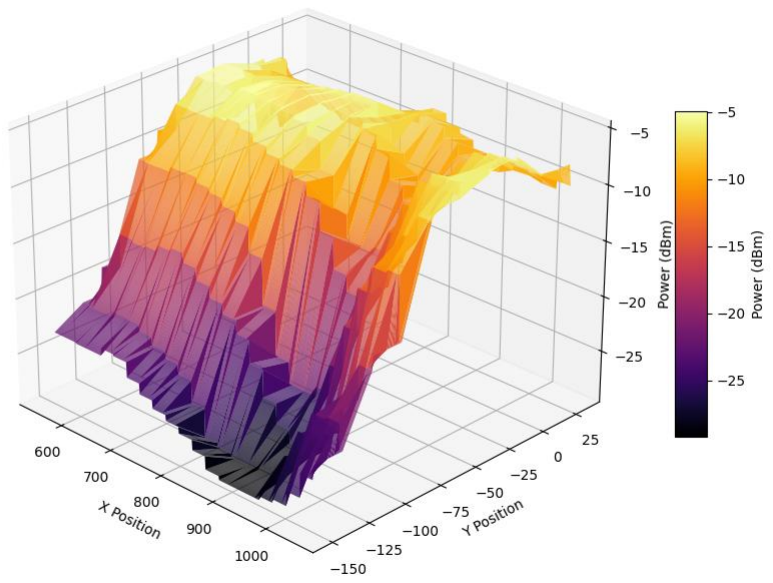
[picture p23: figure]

From Figure 25 the 3D representation of the data shows the difference in power values observed in a more intuitive way. The large trough that exists where the scan started in contrasts to the peak power it ended up settling on with this being much greater in stature. This 3D representation also once again shows how steep the climb from lower power to higher power regions. This shows once more how sensitive the system can be to X-Y inputs through the stepper motors and further reinforces the need for such tight control of this alignment process.

25 15 3D Representation of the Power Observed Over the Raster Scan AreaFigure 25 16 3D Representation of the Power Observed Over the Raster Scan Area

Figure 25 3D representation of raster scan

## Spiral Scan

The data for the spiral scan alignment method that the algorithm made use of was also plotted allowing for closer evaluation of the scan and how successful it is. The data was once again plotted with annotations for the peak and minimum powers as well as the start point being labelled.

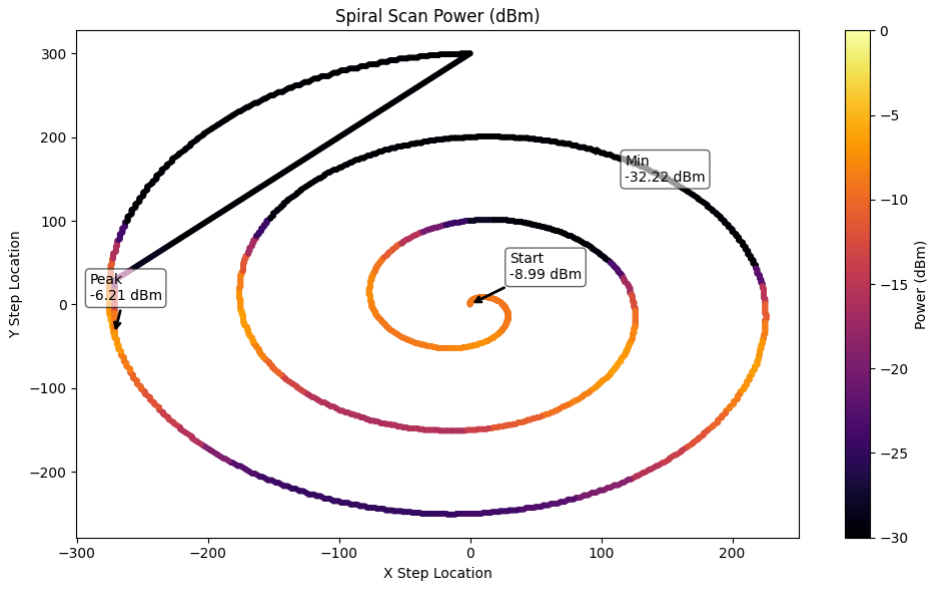
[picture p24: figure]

From Figure 26 the spiral scan algorithm can be visualised showing differing values for the measured power within the fibre over the course of various locations along X and Y directions within this spiral shape. The X-step locations cover a range of 550 steps and the Y-step locations similarly travel 550 steps from top to bottom. The spiral scan starts at the centre with a reasonable value of -8.99 dBm, which is quite a reasonable value for power. The scan then rotates clockwise, with the radius of these rotations increasing each time to cover more distance within the flexure’s movement capabilities. The power can be seen to drop with the extremities of the Y-step location at 300 and -250, respectively. The minimum value for power is measured at this location as being a very poor value of -32.22 dBm, which represents a complete loss in alignment from the fibres, with them receiving virtually no power. The extremities of the x-step locations, however, appear to be more beneficial with the peak power appearing at the farthest point in the negative-x direction, seeing the peak power of -6.21 dBm. What this algorithm shows is that a thin band of high power seemingly exists throughout the central belt of the spiral.

Figure 26 Results of the Spiral Scan Algorithm Starting at a Power Reading of -8.99dBm Observing a Minimum of -32.23dBm and Finding a Peak of -6.21dBm

This shows, as did the raster scan, that the alignment of fibres is very sensitive to small changes with small departures from this medium results in an almost complete loss of power.

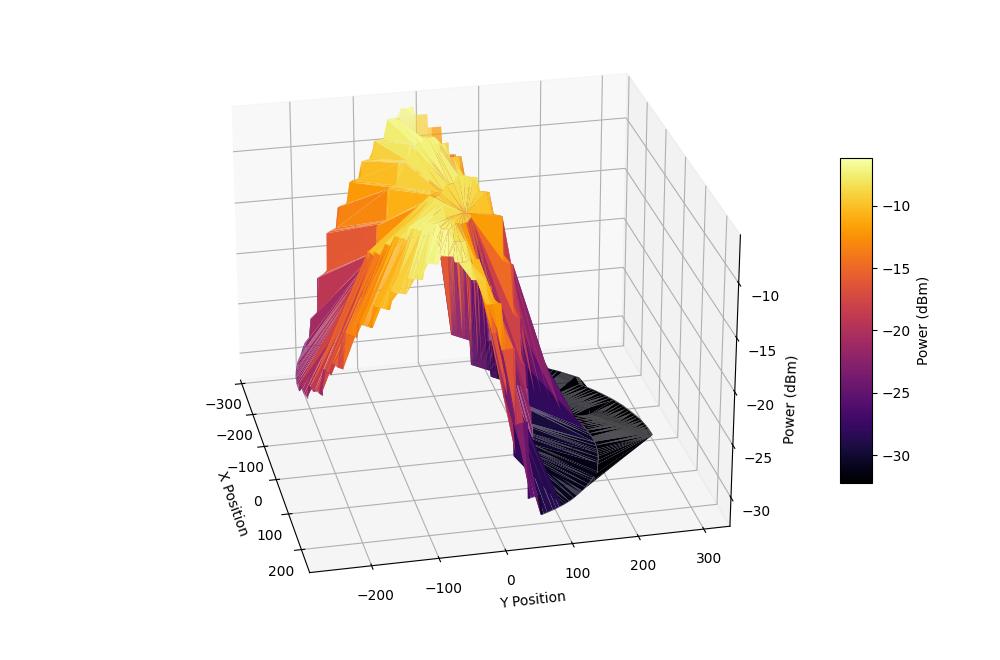
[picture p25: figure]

Figure 27 3D Representation of the Power Observed Over the Spiral Scan Area

The 3D representation helps to better visualise this central belt in the x-direction at around the origin of Y where high power is attainable. The lower regions of power are also witnessed at the extremities of the Y-direction as previously shown.
This scan does not look as comprehensive as the raster scan and results in a more wide-reaching scan of the area. This could be further improved by having several spirals with each starting at the subsequent point of peak power and searching to see if there is further power to be attained within the immediate region. These spirals could also decrease in radius and become finer in their resolution to further increase their comprehensiveness when searching for power.

## Conclusions

The Design Special Project proved to be a successful and practical exploration of a real-world challenge—addressing misalignment issues in Free Space Optics (FSO) communication systems. The project encompassed mechanical design and testing, PCB design and testing, software development, and laboratory-based experimentation.
The mechanical system was largely successful with extremely precise and fine movement of the optical fibre in both the X- and Y-axes. This is essential when aligning optical communication systems, where the alignment is extremely sensitive to small changes. By utilising a very shallow lead screw and stepper motors small adjustments of 0.666μm being achievable. The mechanics of this XY motorised flexure system were comprehensively explained so that it could be understood. It was also important to have the capacity for movements in the Z-direction so that the gap between the fibre and lens could be increased or decreased. The benefits that increasing this gap between the fibre and lens, and therefore increasing the size of the beam, has on the stability of the network connection were explained. The mechanical system for altering the Z-axis was shown with a fixed nut system being utilised to convert rotational movement from the threaded driveshaft into lateral movement capable of moving the XY flexure. Improvements to this would include reducing the scale of the Z-axis movement system. Also, by adding end stops to the X and Y flexure where the lead screws move the fibre would make using the system a lot easier. At current issues exist with these screws or the bushing the exist in unthreading themselves which then requires manual attention to the system.
Both the raster and spiral algorithms were implemented with much success. The raster algorithm showed a very fine scan, which systematically moves upwards in a serpentine pattern, finding the power at each of the steps that the motors take. The spiral algorithm starts at the centre and does large sweeping circles, again evaluating the power at each of these points. The results of these scans show how sensitive the power readings are to changes to the alignment of the fibres, with large peaks and troughs being seen very close to one another. Both algorithms show that they can evaluate the power at each of the steps and find the peak power before travelling back to the highest point of power. This is a major benefit that this has over manual alignment of the optical system, as this algorithm can have a precise memory of where the point of highest power is.
In summary, the project successfully integrated multidisciplinary engineering principles with the objective to deliver a viable and practical solution for improving alignment and performance in FSO systems.

## Individual Contribution – Kyle Watt

PCB Design:
I designed the PCB and made decisions on the necessary components and their implementation. I created all the schematics, Gerbers and required production files to manufacture the PCB. All of which can be seen here: https://github.com/KyleWatt/DST_Laser_Alignment
I also began debugging the PCB, but I ran out of time to properly debug the PCB as I focused my efforts on the software debugging, design and implementation.
Software:
I designed and implemented all the software for this project. That included all the main functionality, movement, algorithms and power reading. All of the code I wrote can be seen here: https://github.com/KyleWatt/DSTLaserAlignmentCode

## Individual Contribution – Rory Mullen

At an early stage was responsible for looking into what components were to be used for the hardware part of the project. This included reading various datasheets to match component operation to the requirements of the system. Main components found were the stepper motors and the motor drivers. Also investigated the voltage regulator for the PCB.
Did large sections of the mechanical design including the various components that make up the mechanical system. This included a few iterations of the Z-axis bracket which was essential due to a switch in concept at a later stage.
Breadboarded and prototype the stepper motor drivers and raspberry pi pico 2 which were ultimately used to test the algorithms Kyle had made.

## Individual Contribution – Tamim Abdul Maleque

I was involved in the selection of components in the early stages of the project. This involved few research work for the MCU choice, looking through different vendors and ultimately choosing RP2350 – because of its availability as Pi Pico 2 (cheap too).
I did the purchases of the components and sourcing of items (for prototyping) with help from my team members. Except for PCB order which was done by Kyle.

Did minimum mechanical design, which was mostly done by Rory, but got involved in the laboratory assembly.
Not my best contribution within a team project, personally, but did do a bit of research work. Need to have a more proactive attitude in the projects for the future.

## References

[1] OECD (2023). Digital. [online] OECD. Available at: https://www.oecd.org/en/topics/digital.html
[2] ITU (2023). Press release : Population of global offline continues steady decline to 2.6 billion people in 2023. [online] ITU. Available at: https://www.itu.int/en/mediacentre/Pages/PR-2023-09-12-universal-and-meaningful-connectivity-by-2030.aspx (https://www.itu.int/en/mediacentre/Pages/PR-2023-09-12-universal-and-meaningful-connectivity-by-2030.aspx)
[3] Lavery, M.P.J. et al. (2018) ‘Tackling Africa’s digital divide’, Nature Photonics, 12(5), pp. 249–252. https://doi.org/10.1038/s41566-018-0162-z
[4] Trichili, A., Cox, M.A., Ooi, B.S. and Alouini, M.-S. (2020). Roadmap to free space optics. Journal of the Optical Society of America B, 37(11), p.A184. doi: https://doi.org/10.1364/josab.399168
[5] Wikipedia Contributors (n.d.). Shannon–Hartley theorem. [online] Wikipedia. Available at: https://en.wikipedia.org/wiki/Shannon%E2%80%93Hartley_theorem
[6] Abadi, M.M., Cox, M.A., Alsaigh, R.E. et al. A space division multiplexed free-space-optical communication system that can auto-locate and fully self align with a remote transceiver. Sci Rep 9, 19687 (2019). https://doi.org/10.1038/s41598-019-55670-1
[7] Newport (n.d.). Technical Notes : Optical Fiber Alignment. [online] www.newport.com. Available at: https://www.newport.com/n/fiber-alignment
[8] Allegro Microsystems. (2017). A4988: DMOS Microstepping Driver with Translator and Overcurrent Protection. [online] Available at: https://www.mouser.co.uk/pdfDocs/A4988-Datasheet.pdf
[9] 28BYJ-48 – 5V Stepper Motor Datasheet. [online] Available at: https://components101.com/sites/default/files/component_datasheet/28byj48-step-motor-datasheet.pdf (https://components101.com/sites/default/files/component_datasheet/28byj48-step-motor-datasheet.pdf)
[10] Raspberry Pi (2024). Hardware design with RP2350: Using RP2350 microcontrollers to build boards and products. [online] Available at: https://datasheets.raspberrypi.com/rp2350/hardware-design-with-rp2350.pdf

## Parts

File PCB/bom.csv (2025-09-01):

Designator | Footprint | Quantity | Value | LCSC Part #
C1, C15, C23, C31, C39, C47, C55, C63, C71, C79, C87, C95 | 0603 | 12 | 0.22 µF
C10, C11, C115, C116, C12, C13, C16, C18, C20, C21, C24, C26, C28, C29, C32, C34, C36, C37, C40, C42, C44, C45, C48, C5, C50, C52, C53, C56, C58, C60, C61, C64, C66, C68, C69, C72, C74, C76, C77, C80, C82, C84, C85, C88, C9, C90, C92, C93, C96, C98 | 0603 | 50 | 0.1 µF
C100, C101 | 0402 | 2 | 1u
C102, C103 | 0402 | 2 | 10n
C104, C105, C106, C107, C108, C109, C111, C3 | 0402 | 8 | 100n
C110, C112, C113, C114 | 0402 | 4 | 4.7u
C14, C17, C19, C22, C25, C27, C30, C33, C35, C38, C41, C43, C46, C49, C51, C54, C57, C59, C6, C62, C65, C67, C7, C70, C73, C75, C78, C8, C81, C83, C86, C89, C91, C94, C97, C99 | 0603 | 36 | 10nF
C2, C4 | 0402 | 2 | 15p
D1, D2 | DIOM5436X244N | 2 | D_Schottky
D3, D4 | PESD5V0S1BL315 | 2 | PTVS3V3D1BALYL
D5, D7 | LEDC2012X70N | 2 | 5988170107F
D6 | LED_KT-0603R | 1 | KT-0603R
J1 | PHOENIX_1727010 | 1 | 1727010
J10, J11, J12, J15, J16, J17, J4, J5, J6, J7, J8, J9 | HDRV5W62P0X254_1X5_1270X240X1624P | 12 | 77311-462K05LF
J13 | XKB_DC-005-5A-2.0 | 1 | DC-005-5A-2.0
J14 | TE_1981568-1 | 1 | 1981568-1
J2 | TE_5-146280-3 | 1 | 5-146280-3
J3 | AMPHENOL_20021121-00020C4LF | 1 | 20021121-00020C4LF
L1 | 0402 | 1 | 3.3u
L2 | 0805 | 1 | 47uH
R10, R100, R102, R103, R104, R105, R106, R108, R11, R110, R111, R112, R113, R114, R115, R13, R14, R16, R18, R19, R20, R21, R22, R24, R26, R27, R28, R29, R30, R32, R34, R35, R36, R37, R38, R40, R42, R43, R44, R45, R46, R48, R50, R51, R52, R53, R54, R56, R58, R59, R6, R60, R61, R62, R64, R66, R71, R72, R78, R81, R84, R86, R87, R88, R89, R90, R92, R94, R95, R96, R97, R98 | 0805 | 72 | 10k
R101, R107, R109, R15, R17, R23, R25, R31, R33, R39, R41, R47, R49, R55, R57, R63, R65, R8, R83, R85, R9, R91, R93, R99 | 0805 | 24 | 0.2
R3 | 0805 | 1 | 0
R4, R5, R69 | 0805 | 3 | 1k
R67, R68 | 0402 | 2 | 27
R70 | 0805 | 1 | 33
R73, R74, R75 | 0402 | 3 | 10k
R76, R77 | 0805 | 2 | DNF
R79 | 0805 | 1 | 60
R80 | 0402 | 1 | 60
R82 | 0402 | 1 | 100
S1 | SW_100SP1T2B4M7QE | 1 | 100SP1T2B4M7QE
SW1, SW2 | SPEH110101 | 2 | SW_Push
SW3 | SW_219-3LPSTR | 1 | 219-3LPSTR
TP1, TP10, TP11, TP12, TP2, TP3, TP8, TP9 | TestPoint_Pad_2.0x2.0mm | 8 | TestPoint
U1 | QFN-80-1EP_10x10mm_P0.4mm_EP3.4x3.4mm_ThermalVias | 1 | RP2350B-QFN80
U10, U11, U12, U13, U14, U15, U4, U5, U6, U7, U8, U9 | QFN28G_0.5-5X5MM | 12 | DRIVER-A4988SETTR-T_QFN28_ | A4988SETTR-T
U16 | SOIC8-1.27-5X4MM | 1 | PMIC-AP1509-SG-13_SOIC8_ | AP1509-SG-13
U2 | ABM8-272-T3 | 1 | ABM8-272-T3
U3 | SOIC127P790X216-8N | 1 | W25Q128JVSIQ

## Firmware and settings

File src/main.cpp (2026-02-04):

#include <stdio.h>
#include <stdlib.h>
#include <string.h>
#include <ctype.h>
#include "pico/stdlib.h"
#include "Stepper.hpp" 
#include "Raster.hpp" 
#include "Power.hpp"
#include "Spiral.hpp"
#include "SPGD.hpp"
#include "Automation.hpp"


#define UART_ID uart1
#define BAUD_RATE 115200

#define UART_TX_PIN 4
#define UART_RX_PIN 5
#define NUM_READINGS 7

#define MAX_MESSAGE_LENGTH 40

static optic_t* optics[4];
static optic_t opticA;
static optic_t opticB;
static optic_t opticC;
static optic_t opticD;


static int num_held_optics = 2; // Default: hold 2 optics
static float auto_threshold = 20.0; // Default threshold
static int auto_iterations = 10;


typedef enum {
    MODE_MAIN,
    MODE_MANUAL,
    MODE_AUTOMATIC
} ControlMode;


ControlMode current_mode = MODE_MAIN;

void reset_buffer(char *buffer, size_t length) {
    memset(buffer, 0, length);
}


void optics_init() {
    optic_motors_init(&opticA, OPTIC_A);
    optic_motors_init(&opticB, OPTIC_B);
    optic_motors_init(&opticC, OPTIC_C);
    optic_motors_init(&opticD, OPTIC_D);

    optics[0] = &opticA;
    optics[1] = &opticB;
    optics[2] = &opticC;
    optics[3] = &opticD;
}


char *my_strdup(const char *src) {
    if (!src) return NULL;
    size_t len = strlen(src) + 1;
    char *dup = (char *)malloc(len);
    if (dup) {
        memcpy(dup, src, len);
    }
    return dup;
}

int is_valid_number(const char *str) {
    if (!str || *str == '\0') return 0;
    while (*str) {
        if (!isdigit(*str++)) return 0;
    }
    return 1;
}



void process_manual_command(const char *message) {
    char *msg_copy = my_strdup(message);
    char *token = strtok(msg_copy, " ");

    if (token != NULL) {
        if (strcmp(token, "move") == 0) {
            char *optic_select_char = strtok(NULL, " ");
            char *axis = strtok(NULL, " ");
            char *stepsStr = strtok(NULL, " ");

            if (optic_select_char && axis && stepsStr &&
                is_valid_number(optic_select_char) &&
                is_valid_number(stepsStr)) {

                uint steps = atoi(stepsStr);
                uint optic_select_int = atoi(optic_select_char);

                if (optic_select_int > 3) {
                    printf("Error: Optic index must be 0 to 3.\n");
                } else if (strcmp(axis, "x") == 0) {
                    printf("MOVING optic %u X by %u steps\n", optic_select_int, steps);
                    optics[optic_select_int]->motor_X.target_steps = steps;
                    optics[optic_select_int]->motor_X.moving = true;
                    motors_move(optics);
                } else if (strcmp(axis, "y") == 0) {
                    printf("MOVING optic %u Y by %u steps\n", optic_select_int, steps);
                    optics[optic_select_int]->motor_Y.target_steps = steps;
                    optics[optic_select_int]->motor_Y.moving = true;
                    motors_move(optics);
                } else if (strcmp(axis, "z") == 0) {
                    printf("MOVING optic %u Z by %u steps\n", optic_select_int, steps);
                    optics[optic_select_int]->motor_Z.target_steps = steps;
                    optics[optic_select_int]->motor_Z.moving = true;
                    motors_move(optics);
                } else {
                    printf("Error: Unknown axis '%s'. Use 'x' or 'y' or 'z'.\n", axis);
                }
            } else {
                printf("Error: Invalid move format. Usage: move <optic 0-3> x/y/z <steps>\n");
            }

        } else if (strcmp(token, "set") == 0) {
            char *optic_select_char = strtok(NULL, " ");
            char *axis = strtok(NULL, " ");
            char *dir = strtok(NULL, " ");

            if (optic_select_char && axis && dir &&
                is_valid_number(optic_select_char) &&
                is_valid_number(dir)) {

                uint direction = atoi(dir);
                uint optic_select_int = atoi(optic_select_char);

                if (optic_select_int > 3) {
                    printf("Error: Optic index must be 0 to 3.\n");
                } else if (strcmp(axis, "x") == 0) {
                    optics[optic_select_int]->motor_X.direction = direction;
                    printf("Set optic %u X direction to %u\n", optic_select_int, direction);
                } else if (strcmp(axis, "y") == 0) {
                    optics[optic_select_int]->motor_Y.direction = direction;
                    printf("Set optic %u Y direction to %u\n", optic_select_int, direction);
                } else if (strcmp(axis, "z") == 0) {
                    optics[optic_select_int]->motor_Z.direction = direction;
                    printf("Set optic %u Z direction to %u\n", optic_select_int, direction);
                } else {
                    printf("Error: Unknown axis '%s'. Use 'x' or 'y' or 'z'.\n", axis);
                }
            } else {
                printf("Error: Invalid set format. Usage: set <optic 0-3> x/y/z <0/1>\n");
            }

        } else if (strcmp(token, "setcentre") == 0) {
            char *optic_select_char = strtok(NULL, " ");
            if (optic_select_char && is_valid_number(optic_select_char)){
                uint optic_select_int = atoi(optic_select_char);
                set_center(optics[optic_select_int]);
            }
        } else if (strcmp(token, "centre") == 0) {
            center_optic(optics);
        } else if (strcmp(token, "location") == 0) {
            printf("X = %d Y = %d Z = %d \n",optics[0]->x_location,optics[0]->y_location, optics[0]->z_location);
        } else if (strcmp(token, "direction") == 0) {
            printf("Xdir = %d Ydir = %d Zdir = %d \n",optics[0]->motor_X.direction,optics[0]->motor_Y.direction, optics[0]->motor_Z.direction);
        } else if (strcmp(token, "exit") == 0) {
            printf("Exiting manual mode.\n");
            current_mode = MODE_MAIN;

        } else if (strcmp(token, "help") == 0) {
            printf("Manual Mode Commands:\n");
            printf("  move <optic 0-3> <x|y|z> <steps>     - Move selected motor by step count\n");
            printf("     e.g., move 0 x 100\n");
            printf("  set <optic 0-3> <x|y|z> <0|1>        - Set direction of motor (0: one way, 1: other)\n");
            printf("     e.g., set 2 y 1\n");
            printf("  setcentre <optic 0-3>               - Set current position as center for optic\n");
            printf("     e.g., setcentre 1\n");
            printf("  centre <optic 0-3>                  - Move optic to its center position\n");
            printf("     e.g., centre 3\n");
            printf("  exit                                - Return to main command mode\n");
            printf("  help                                - Show this help message\n");
        } else {
            printf("Unknown manual command: %s\n", token);
        }
    } 

    free(msg_copy);
}


void process_main_command(const char *message) {
    char *msg_copy = my_strdup(message);
    char *token = strtok(msg_copy, " ");

    if (token != NULL) {
        if (strcmp(token, "manual") == 0) {
            printf("Entering manual mode...\n");
            current_mode = MODE_MANUAL;

        } else if (strcmp(token, "raster") == 0) {
            // Parse optional arguments
            char *heightStr = strtok(NULL, " ");
            char *widthStr = strtok(NULL, " ");
            char *interatrionsStr = strtok(NULL, " ");
            char *ydirStr = strtok(NULL, " ");

            // If user provides values and they are valid numbers, update them
            if (heightStr && widthStr && interatrionsStr && ydirStr &&
                is_valid_number(heightStr) &&
                is_valid_number(widthStr) &&
                is_valid_number(interatrionsStr)&&
                is_valid_number(ydirStr)) {

                int height = atoi(heightStr);
                int width = atoi(widthStr);
                int iterations = atoi(interatrionsStr);
                uint ydir = atoi(ydirStr);
                printf("Starting Raster Scan with height=%d, width=%d, iterations=%d\n", height, width, iterations);
                start_raster(optics, height, width, iterations, ydir);
            } else if (heightStr || widthStr || interatrionsStr) {
                printf("Invalid raster parameters. Usage: raster [height width iterations]\n");
                free(msg_copy);
                return;
            }

        } else if (strcmp(token, "spiral") == 0) {
            printf("Starting Spiral\n");
            // Parse optional arguments
            //int turns, int spiral_spacing, int iterations
            char *turnsStr = strtok(NULL, " ");
            char *spacingStr = strtok(NULL, " ");
            char *interatrionsStr = strtok(NULL, " ");

            // If user provides values and they are valid numbers, update them
            if (turnsStr && spacingStr && interatrionsStr &&
                is_valid_number(turnsStr) &&
                is_valid_number(spacingStr) &&
                is_valid_number(interatrionsStr)) {

                int turns = atoi(turnsStr);
                int spacing = atoi(spacingStr);
                int interactions = atoi(interatrionsStr);
                printf("Starting Spiral with turns=%d, width=%d, interactions=%d\n", turns, spacing, interactions);
                start_spiral(optics, turns, spacing, interactions);

            } else if (turnsStr || spacingStr || interatrionsStr) {
                printf("Invalid raster parameters. Usage: raster [turns spacing iterations]\n");
                free(msg_copy);
                return;
            }
        else if (strcmp(token, "hold") == 0) {
            char *stroptic = strtok(NULL, " ");
            int optic = atoi(stroptic);
            optics[optic]->hold_position = true;
            printf("Setting optic %d to hold position\n", optic);

        }
        else if (strcmp(token, "automatic") == 0) {
            float threshold = 20.0; // Example threshold value
            printf("Entering automatic mode...\n");
            current_mode = MODE_AUTOMATIC; 
            
        }
        else if (strcmp(token, "exit") == 0) {
            printf("Main mode.\n");
            current_mode = MODE_MAIN;

        }
        } else if (strcmp(token, "help") == 0) {
            printf("Main Mode Commands:\n");
            printf("  manual                        - Enter manual control mode\n");
            printf("  raster [h w i y]              - Start raster scan (height, width, iterations, y direction)\n");
            printf("     e.g., raster 5 5 3 1\n");
            printf("  spiral [t s i]                - Start spiral scan (turns, spacing, iterations)\n");
            printf("     e.g., spiral 3 2 4\n");
            printf("  power                         - Read current power levels\n");
            printf("  hold <optic 0-3>              - Set an optic to hold position (static)\n");
            printf("  setheld <number 0-4>          - Set number of optics to hold (highest power optics will be held)\n");
            printf("  automatic                     - Enter automatic search mode\n");
            printf("     - In automatic mode, the system continuously searches for higher power on non-held optics.\n");
            printf("     - Held optics are those with the highest power, as set by 'setheld'.\n");
            printf("     - Search parameters adapt over time for global and local optimization.\n");
            printf("     - After each search cycle, held/searching optics are updated based on power values.\n");
            printf("     - You can exit automatic mode at any time by typing 'exit'.\n");
            printf("  exit                          - Return to main command mode\n");
            printf("  help                          - Show this help message\n");
        }else if (strcmp(token, "power") == 0) {
            printf("Checking power...\n");
            power_t current_power = get_latest_power();

            printf("Current Power: A=%.2f, B=%.2f, C=%.2f, D=%.2f\n",
                current_power.power_A,
                current_power.power_B,
                current_power.power_C,
                current_power.power_D);
        } else {
            printf("Unknown main command: %s\n", token);
        }
    }

    free(msg_copy);
}

void process_auto_command(const char *message) {
    char *msg_copy = my_strdup(message);
    char *token = strtok(msg_copy, " ");

    if (token != NULL) {
        if (strcmp(token, "exit") == 0) {
            printf("Entering manual mode...\n");
            current_mode = MODE_MAIN;

        }else if (strcmp(token, "setheld") == 0) {
            char *numStr = strtok(NULL, " ");
            if (numStr && is_valid_number(numStr)) {
                int num = atoi(numStr);
                if (num >= 0 && num <= 4) {
                    num_held_optics = num;
                    printf("Number of held optics set to %d\n", num_held_optics);
                } else {
                    printf("Error: Number must be between 0 and 4.\n");
                }
            } else {
                printf("Usage: setheld <number 0-4>\n");
            }
        } else if (strcmp(token, "setiterations") == 0) {
            char *numStr = strtok(NULL, " ");
            if (numStr && is_valid_number(numStr)) {
                auto_iterations = atoi(numStr);
            }
        } else if (strcmp(token, "setthreshold") == 0) {
            char *numStr = strtok(NULL, " ");
            if (numStr && is_valid_number(numStr)) {
                auto_iterations = atof(numStr);
            }
        }
    }
}



void handle_serial_input(void (*command_handler)(const char *)) {
    static char message[MAX_MESSAGE_LENGTH];
    static unsigned int message_pos = 0;

    int c = getchar_timeout_us(0); // Non-blocking read

    if (c != PICO_ERROR_TIMEOUT) {
        if (c != '\n' && c != '\r' && message_pos < MAX_MESSAGE_LENGTH - 1) {
            message[message_pos++] = (char)c;
        } else if (c == '\n' || c == '\r') {
            message[message_pos] = '\0';
            if (message_pos > 0) {
                printf("Received: %s\n", message);
                command_handler(message);
            }
            message_pos = 0;
            reset_buffer(message, MAX_MESSAGE_LENGTH);
        }
    }
}

int main() {
    stdio_init_all();
    optics_init();
    initPower();

    printf("System ready. Type 'help' for available commands.\n");


    auto_parameters_t passive_parameters, agressive_parameters;
    while (true) {
        if (current_mode == MODE_MAIN) {
            handle_serial_input(process_main_command);
        } else if (current_mode == MODE_MANUAL) {
            handle_serial_input(process_manual_command);
        } else if (current_mode == MODE_AUTOMATIC) {
            handle_serial_input(process_auto_command);
            auto_search_loop(optics,num_held_optics,auto_threshold,auto_iterations,passive_parameters,agressive_parameters);
            sleep_ms(500); 
        }
    }

    return 0;
}

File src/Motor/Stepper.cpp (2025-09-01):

#include "stepper.hpp"
#include "Power.hpp"
#include "pico/time.h"
#include "pico/stdlib.h"
#include <math.h>
#include <stdio.h>
#include <cstdlib>
#include "pico/multicore.h"
 
#define HOLD_TIME 500
 
void optic_motors_init(optic_t* optic, optic_select_t optic_select) {
    // Setup the motor struct
    switch (optic_select) {
    case OPTIC_A:
        //OPTIC A ---------------------------
        //Setting X motor
        optic->motor_X.pin_step      = STEP1_PIN;
        optic->motor_X.pin_dir       = DIR1_PIN;
        //Setting Y motor
        optic->motor_Y.pin_step      = STEP2_PIN;
        optic->motor_Y.pin_dir       = DIR2_PIN;
        //Setting Z motor
        optic->motor_Z.pin_step      = STEP3_PIN;
        optic->motor_Z.pin_dir       = DIR3_PIN;
        break;
    case OPTIC_B:
        //OPTIC B ---------------------------
        //Setting X motor
        optic->motor_X.pin_step      = STEP4_PIN;
        optic->motor_X.pin_dir       = DIR4_PIN;
        //Setting Y motor
        optic->motor_Y.pin_step      = STEP5_PIN;
        optic->motor_Y.pin_dir       = DIR5_PIN;
        //Setting Z motor
        optic->motor_Z.pin_step      = STEP6_PIN;
        optic->motor_Z.pin_dir       = DIR6_PIN;
        break;
    case OPTIC_C:
        //OPTIC C ---------------------------
        //Setting X motor
        optic->motor_X.pin_step      = STEP7_PIN;
        optic->motor_X.pin_dir       = DIR7_PIN;
        //Setting Y motor
        optic->motor_Y.pin_step      = STEP8_PIN;
        optic->motor_Y.pin_dir       = DIR8_PIN;
        //Setting Z motor
        optic->motor_Z.pin_step      = STEP9_PIN;
        optic->motor_Z.pin_dir       = DIR9_PIN;
        break;
    case OPTIC_D:
        //OPTIC D ---------------------------
        //Setting X motor
        optic->motor_X.pin_step      = STEP10_PIN;
        optic->motor_X.pin_dir       = DIR10_PIN;
        //Setting Y motor
        optic->motor_Y.pin_step      = STEP11_PIN;
        optic->motor_Y.pin_dir       = DIR11_PIN;
        //Setting Z motor
        optic->motor_Z.pin_step      = STEP12_PIN;
        optic->motor_Z.pin_dir       = DIR12_PIN;
        break;
    }
 
    // Init motor variables
    optic->motor_X.direction = 0;
    optic->motor_Y.direction = 0;
    optic->motor_Z.direction = 0;
    optic->motor_X.cur_steps = 0;
    optic->motor_Y.cur_steps = 0;
    optic->motor_Z.cur_steps = 0;
    optic->motor_X.target_steps = 0;
    optic->motor_Y.target_steps = 0;
    optic->motor_Z.target_steps = 0;
    optic->motor_X.moving = false;
    optic->motor_Y.moving = false;
    optic->motor_Z.moving = false;
    optic->x_location = 0;
    optic->y_location = 0;
    optic->z_location = 0;
    optic->max_x_location = 0;
    optic->max_y_location = 0;
    optic->max_z_location = 0;
    optic->pin_enable = ENABLE_N;
    optic->moving = false;
    optic->max_power = 0;
 
    // Initialise the GPIO
    gpio_init(optic->motor_X.pin_dir);
    gpio_init(optic->motor_Y.pin_dir);
    gpio_init(optic->motor_Z.pin_dir);
    gpio_init(optic->motor_X.pin_step);
    gpio_init(optic->motor_Y.pin_step);
    gpio_init(optic->motor_Z.pin_step);
    gpio_init(optic->pin_enable);
    gpio_set_dir(optic->motor_X.pin_dir, GPIO_OUT);
    gpio_set_dir(optic->motor_Y.pin_dir, GPIO_OUT);
    gpio_set_dir(optic->motor_Z.pin_dir, GPIO_OUT);
    gpio_set_dir(optic->motor_X.pin_step, GPIO_OUT);
    gpio_set_dir(optic->motor_Y.pin_step, GPIO_OUT);
    gpio_set_dir(optic->motor_Z.pin_step, GPIO_OUT);
    gpio_set_dir(optic->pin_enable, GPIO_OUT);
}
 
void enable_motors(optic_t* optic) {
    gpio_put(optic->pin_enable, 0);
}
 
void disable_motor(optic_t* optic) {
    gpio_put(optic->pin_enable, 1);
}

void set_max_pos(optic_t* optic, float power) {
    // Track max power and position for each optic
    if (power > optic->max_power) {
        optic->max_power = power;
        optic->max_x_location = optic->x_location;
        optic->max_y_location = optic->y_location;
    }
}

void go_to_max_pos(optic_t* optics[]) {
    for (int i = 0; i < 4; i++) {
        // Calculate steps needed to return to max position
        int x_steps = abs(optics[i]->x_location - optics[i]->max_x_location);
        int y_steps = abs(optics[i]->y_location - optics[i]->max_y_location);

        // Set X direction and steps
        optics[i]->motor_X.direction = (optics[i]->x_location < optics[i]->max_x_location) ? 1 : 0;
        optics[i]->motor_X.target_steps = x_steps;
        optics[i]->motor_X.moving = (x_steps > 0);

        // Set Y direction and steps
        optics[i]->motor_Y.direction = (optics[i]->y_location < optics[i]->max_y_location) ? 1 : 0;
        optics[i]->motor_Y.target_steps = y_steps;
        optics[i]->motor_Y.moving = (y_steps > 0);
    }
    motors_move(optics);
}

void set_direction(optic_t* optics[]) {
    for (uint i = 0; i < 4; i++) {
        optic_t* optic = optics[i];
        if (optic->motor_X.direction != gpio_get(optic->motor_X.pin_dir)) {
            gpio_put(optic->motor_X.pin_dir, optic->motor_X.direction);
        }
        if (optic->motor_Y.direction != gpio_get(optic->motor_Y.pin_dir)) {
            gpio_put(optic->motor_Y.pin_dir, optic->motor_Y.direction);
        }
        if (optic->motor_Z.direction != gpio_get(optic->motor_Z.pin_dir)) {
            gpio_put(optic->motor_Z.pin_dir, optic->motor_Z.direction);
        }
    }
    sleep_us(1);
}
 
void set_low(optic_t* optics[]) {
    for (uint i = 0; i < 4; i++) {
        optic_t* optic = optics[i];
        gpio_put(optic->motor_X.pin_step, 0);
        gpio_put(optic->motor_Y.pin_step, 0);
        gpio_put(optic->motor_Z.pin_step, 0);
    }
}
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

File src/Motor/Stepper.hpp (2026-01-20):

#include "pico/stdlib.h"
#include "pico/multicore.h"

#ifndef STEPPER_HPP
#define STEPPER_HPP

//Motor Step and DIR PINS
//UART PINS take  GPIO 0 and 1
//GPIO 0 is TX and GPIO 1 is RX
#define STEP1_PIN 2
#define DIR1_PIN 3
#define STEP2_PIN 4
#define DIR2_PIN 5
#define STEP3_PIN 6 //NEED TO CHANGE THIS BACK -> JUST HAD TO CHANGE PINS TO MATCH DEV BOARD REAL PINS DIFFRENT
#define DIR3_PIN 7
#define STEP4_PIN 8
#define DIR4_PIN 9
#define STEP5_PIN 10
#define DIR5_PIN 11
#define STEP6_PIN 12
#define DIR6_PIN 13
#define STEP7_PIN 14
#define DIR7_PIN 15
#define STEP8_PIN 16
#define DIR8_PIN 17
#define STEP9_PIN 18
#define DIR9_PIN 19
#define STEP10_PIN 20
#define DIR10_PIN 21
#define STEP11_PIN 22
#define DIR11_PIN 23
#define STEP12_PIN 24
#define DIR12_PIN 25

// Enable Pin
#define ENABLE_N 38

typedef enum {
    MOVING,
    STOPPED
} motor_state_t;

typedef enum {
    AGRESSIVE,
    PASSIVE,
    MAINTAIN,
    START
} search_state_t;

typedef struct {
    // Pins
    uint pin_dir;
    uint pin_step;

    // Motion
    int cur_steps;
    int target_steps;
    int8_t direction;

    bool moving; 
} motor_t;

typedef struct {
    motor_t motor_X;
    motor_t motor_Y;
    motor_t motor_Z;
    search_state_t search;
    int x_location;
    int y_location;
    int z_location;
    float y_pos;
    float x_pos;
    int max_x_location;
    int max_y_location;
    int max_z_location;
    float max_power;
    float cur_power;
    float cost_plust;
    float cost_minus;
    float grad_approx;
    uint pin_enable;
    bool moving;
    bool hold_position;

} optic_t;

typedef enum {
    OPTIC_A,
    OPTIC_B,
    OPTIC_C,
    OPTIC_D,
} optic_select_t;

typedef enum {
    MOTOR_X,
    MOTOR_Y,
    MOTOR_Z,
} motor_axis_t;

void optic_motors_init(optic_t* optic,optic_select_t optic_select);

void update_motor_steps(optic_t* optic, motor_axis_t motor_axis);

void disable_motor(motor_t* motor);

void enable_motor(motor_t* motor);

void motors_move(optic_t** optics);

void set_direction(optic_t optics[]);

void center_optic(optic_t* optics[]);

void set_max(optic_t* optic, motor_axis_t axis_select );

void set_center(optic_t* optic);

void set_max_pos(optic_t* optic, float power);

void go_to_max_pos(optic_t* optics[]);

#endif // STEPPER_HPP

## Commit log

2025-05-01 Inital code for laser alignment though pi pico
2025-05-05 updated stepper code
2025-05-05 added algorithm and changed stepper
2025-05-05 Added motor controls to Algorithm
2025-05-18 Added spiral algorithm, fixed manual controls and fixed stepper
    [Raster.cpp, Spiral.cpp, Stepper.cpp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]
2025-05-20 Added power reading though UART, power is read during algortihm and when max power is found, motors move to that position
2025-05-23 Fixed issues with spiral stepping and power reading
    [Raster.cpp, Spiral.cpp, Stepper.cpp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]
2025-09-01 changes to main
    [DST-B_Cu.gbl, DST-B_Mask.gbs, DST-B_Paste.gbp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]
2025-09-01 added PCB image
2026-01-20 fixed old automated code
    [Automatic.cpp, Power.cpp, SPGD.cpp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]
